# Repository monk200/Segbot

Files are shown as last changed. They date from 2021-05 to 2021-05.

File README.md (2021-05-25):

# Segbot
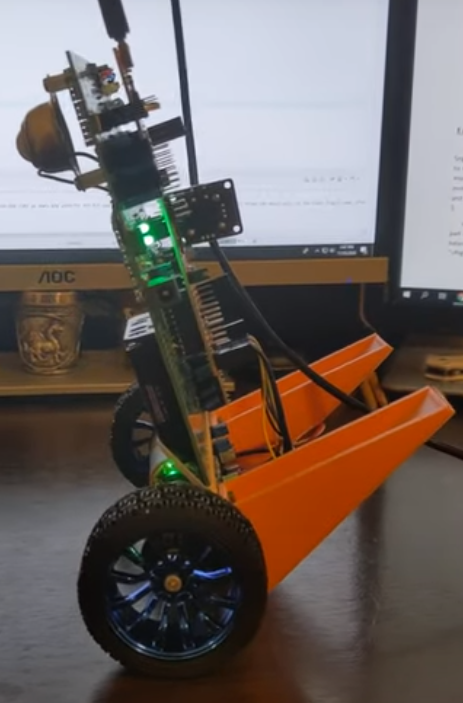
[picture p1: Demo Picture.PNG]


This repository contains files such as code, CAD files, Matlab simulations, and brainstorming documents from my work designing and developing a two-wheeled balancing robot. The project can be split into two main parts: designing the system and developing the real-world version of the system. The original design was done in my [Mechatronics](http://coecsl.ece.illinois.edu/ge423/) course as a final project for Spring 2020 but the real robot was built and programmed in the course [Computer Control of Mechanical Systems](http://coecsl.ece.illinois.edu/me461/) in Fall 2020. Both courses were led by UIUC Prof. Dan Block, the university's Control Systems Lab Manager. Prof. Block created a guide to building a Segbot at [this link](http://coecsl.ece.illinois.edu/segbot/segbot.html) and his guidance and expertise was absolutely essential in all steps of this project.  

## Designing the System
Because of the COVID-19 pandemic, Prof. Block restructured the final project of Mechatronics to be to design a Segbot from scratch. At the time, the [Mechatronics course used the MPS430G2553 microcontroller](https://github.com/monk200/Mechatronics_with_MSP430G2553) so all of the initial design choices and considerations were made keeping that in mind. I compiled a list of parts that were essential for desiging a PCB that would interface with the microcontroller. I was also tasked with creating a CAD model of the robot body and using its parameters, as well as the parameters of the motors, to tune a simulation to balance the Segbot. The last portion of the designing process was to create pseudocode for how the robot needed to behave to balance, solving the inverted pendulum problem. Below you can find a list of each step in the process:  
* [Creating a parts list](https://github.com/monk200/Segbot/blob/main/Parts_Lists/Initial_Parts_List.md): This document includes a list of each part, a link to an online retailor to buy the part, and a link to its datasheet. Most parts also include commentary on the thought process behind choosing the specified part.  
* [Initial wiring configuration](https://github.com/monk200/Segbot/blob/main/Wiring/Initial%20Design%20Wiring%20Diagram.png): This image was created and iterated upon when planning out how the system needs to be connected electronically. This was done as an intermediate step before desiging the PCB in EagleCAD because the color-coding made it quick and easy to troubleshoot and discuss.  
* [PCB design](https://github.com/monk200/Segbot/tree/main/Wiring/Initial%20EagleCAD%20Files): EagleCAD was used to design a PCB that the MSP430 would sit onto. Some parts needed to be created from scratch but otherwise it is a very minimal board.  
* [CAD model](https://github.com/monk200/Segbot/tree/main/Frame/Initial%20Frame%20Design): Autodesk Fusion 360 was used to design a body for the Segbot that would ideally be 3D-printed in UIUC's ISE design lab.  
* [Matlab model](https://github.com/monk200/Segbot/tree/main/Matlab_Simulation/Initial%20Simulation%20Files): A simulation animation and framework were provided by Prof. Block. The parameters from the previous stages of the design process were input into the model and it was manually tuned to balance. This step is useful as a proof-of-concept and as an excersie for students to get experience tuning a control system.  

## Developing the System
While Prof. Block signed off on the original design as feasible, since the second part of this project was done as part of a different course it didn't use the exact same design. Prof. Block upgraded to using the [TMS320F28379D microcontroller](https://github.com/monk200/Mechatronics_with_TMS320F28379D), added a variety of peripherals to the PCB, and simplified the body of the Segbot. For the sake of being thorough, the points below include information on each stage of the design process and how they've changed:  
* [Parts list](https://github.com/monk200/Segbot/blob/main/Parts_Lists/Revised_Parts_List.md): This document lists the essential parts used in the new Segbot design and how they compare to the specs of the previously chosen parts.  
* [Wiring configuration](https://github.com/monk200/Segbot/blob/main/Wiring/Reworked%20Wiring%20Diagram.png): This image is again a color-coded wiring schematic to show a quick layout of how the new components are connected.  
* [PCB design](https://github.com/monk200/Segbot/tree/main/Wiring/Reworked%20EagleCAD%20Files): This folder contains the new EagleCAD files for the PCB. As stated earlier, this is a much more complicated design because a lot of peripherals were added to allow the board to be used for exploring other applications.  
* [CAD model](https://github.com/monk200/Segbot/tree/main/Frame/Reworked%20Frame%20Design): A much simpler design, this design is only two 3D-printed legs to be attached to the PCB itself.  

With a new physical design, the Matlab model needed to be redone but this time since the physical parts were present the tuning was much more reliable. Throughout the [Computer Control of Mechanical Systems](https://github.com/monk200/Mechatronics_with_TMS320F28379D) course, the new microcontroller was explolred and experimented with. Near the end of the semester, I programmed the board to implement control algorithms to solve the inverted pendulum problem and control the robot's motion. The links below lead to details on each step of this process:  
* [Matlab model](https://github.com/monk200/Segbot/tree/main/Matlab_Simulation/Reworked%20SImulation%20Files): Using the same simulation as before but new, more accurate, parameters, I manually tuned the Segbot to balance.  
* [Programming](https://github.com/monk200/Segbot/tree/main/Code): This link goes to the code for the project with extensive details on the processes used and how to set it up on the hardware.  

## Final Product
Below are links to several videos demonstrating different portions of the Segbot's performance:  

### Controlling the Segbot with the Keyboard
Controlling Segbot (https://youtu.be/ZbytxEKrEEE)  
[Github Video Link](https://github.com/monk200/Segbot/blob/main/Working%20Demo%20Video.mp4)  

### Balancing Segbot
Balancing Segbot (https://youtu.be/_FPlLJUeUD4)  

### The Stable Simulation
Stable Simulation (https://youtu.be/3cc0C4fP93k)

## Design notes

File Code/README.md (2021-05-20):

# Programming
This folder finally contains the [code](https://github.com/monk200/Segbot/tree/main/Code/segbot) used to program the TMS320F28379D on Prof. Block's Segbot design to balance and turn accoring to user input through the keyboard. The [code walkthrough](https://github.com/monk200/Segbot/blob/main/Code/code_walkthrough.md) goes through the steps taken to set up the controller and its peripherals as well as a deep focus on the [control algorithms](https://github.com/monk200/Segbot/blob/main/Code/code_walkthrough.md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) used.  

## What the Code Does
As far as the actual code and running it on the Segbot, the only file I personally wrote code in was [segbot_main.c](https://github.com/monk200/Segbot/blob/main/Code/segbot/segbot_main.c), so that's where you can find all of the logic and initializations I've done. It's fairly well commented and organized but the [code walkthrough](https://github.com/monk200/Segbot/blob/main/Code/code_walkthrough.md) includes detailed descriptions, datasheets, and line numbers to guide other people through it. In its current state, the code is set up to balance and turn the Segbot while it is plugged into the computer and being controlled by keyboard inputs. If the microcontroller is flashed and disconnected from the computer, the Segbot will be able to balance but it won't turn (unless you set a constant turn rate in the code, in which case it will continuously spin at that rate).  

## Operating the Segbot
To get the Segbot started, rest it on its legs so the wheels are off the ground and the body is still. Turn the Segbot on by popping the batteries in and then leave it alone to calibrate the sensors for about 4 seconds (a blue LED will be blinking while the sensors calibrate). After this, turn the motors on with the switch and place the Segbot vaguely upright. From there, it will balance itself and be ready to control. Make sure to always turn the motor switch back off before restarting the Segbot.  

## Demo Video
Controlling Segbot (https://youtu.be/ZbytxEKrEEE)

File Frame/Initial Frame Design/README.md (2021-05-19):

# Initial Frame Design
Fusion 360 was used to design the frame, create drawing files, and render images and videos. Since the plan was to 3D print the frame, I wanted to make the dimensions fit inside the ISE product design lab’s Stratasys Dimension SST 1200 3D printer. This means the design had to be smaller than 30x25x25 cm. It also needed to house a battery, the PCB, and account for the motors and wheels. The design ended up being a fairly simple box with pockets inside to be able to set the battery and board into, as well as having front-facing windows to be able to see and quickly access the hardware. The sides of the frame have circular cutouts to fit the motors through and the front and back of the frame have kickstands to keep the Segbot from damaging itself if it fails to balance. The kickstands were highly recommended by Prof. Block because not only do they minimize the damage from the Segbot going off balance but they also provide a stable, repeatable position to calibrate the sensors on startup.  

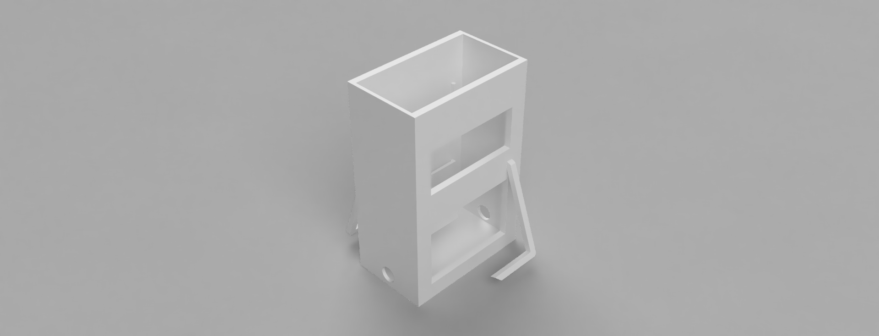
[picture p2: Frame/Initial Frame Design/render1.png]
Render 1
  

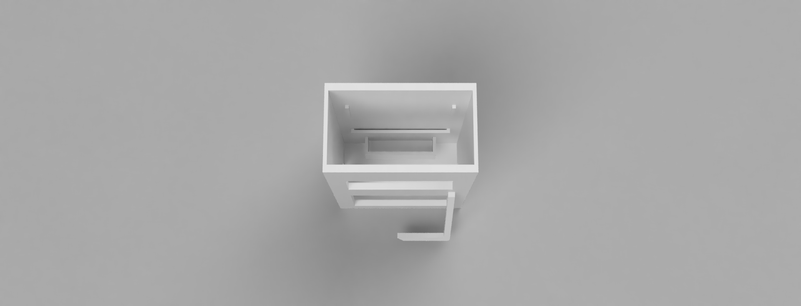
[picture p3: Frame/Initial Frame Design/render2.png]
Render 2
  

## Model Parameters
For the next step of simulating the Segbot in Matlab, the parameters of the physical model will be needed. Fusion provides these and I listed them in [Frame Physical Properties.txt](https://github.com/monk200/Segbot/blob/main/Frame/Initial%20Frame%20Design/Frame%20Physical%20Properites.txt). Below is a summary of the properties:  

* Material:	ABS Plastic
* Mass	1535.286 g
* Center of Mass	-10.00 cm, 13.805 cm, 3.897 cm
* Body Width: 0.20 m
* Body Depth: 0.20 m
* Body Height: 0.29 m
* Distance of the Center of Mass from the Wheel Axis: 11.86 m  

More calculations and their equations will be explained in the [Matlab Model](https://github.com/monk200/Segbot/tree/main/Matlab_Simulation/Initial%20Simulation%20Files) section.

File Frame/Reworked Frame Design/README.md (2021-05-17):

# Reworked Frame Design
Prof. Block simplified the frame design so much so that there isn't really a "frame" left. Instead of designing a protective casing for the hardware, he only designed front-facing legs that the motor subassembly fastens into and then both attach to the PCB. Minimizing the size of this part reduces 3D printer filament needed and makes the Segbot overall more condensed. The battery pack is attached to the back of the PCB by wrapping around the whole thing with a rubber band, which is very secure and manages to not be in the way. Minimizing the design like this also, however, removes the safety of allowing the Segbot to fall backwards when trying to tune the poles. This ended up not being a problem while I was running the program because I always kept a watchful eye on it and used it on smooth, predictable surfaces.  

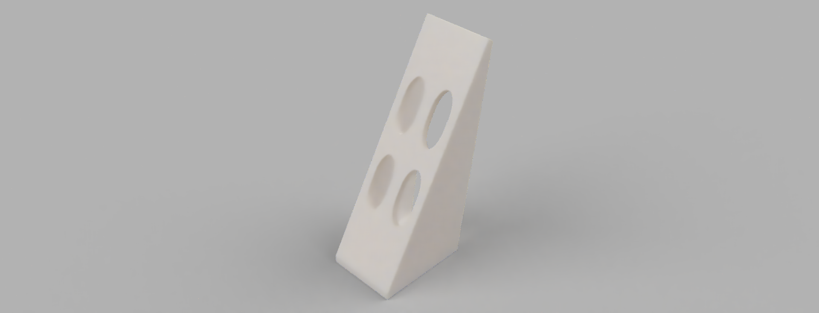
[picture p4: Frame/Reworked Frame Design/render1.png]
Render 1
  

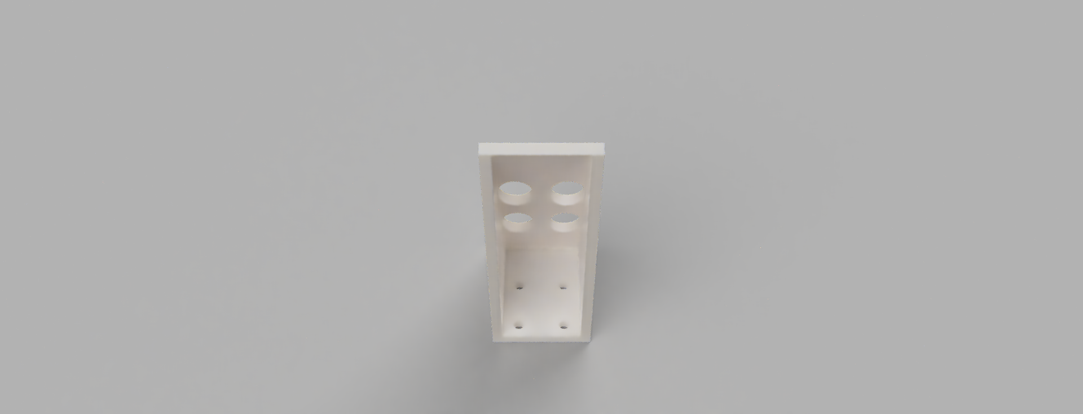
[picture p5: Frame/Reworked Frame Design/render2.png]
Render 2
  

## Model Parameters
For the next step of simulating the Segbot in Matlab, the parameters of the physical model will be needed. Fusion provides these and I listed them in [Frame Physical Properties.txt](https://github.com/monk200/Segbot/blob/main/Frame/Reworked%20Frame%20Design/Frame%20Physical%20Properites.txt). Below is a summary of the properties:  

* Material:	ABS Plastic
* Mass	2.134E+04 g
* Center of Mass	150.00 mm, 319.389 mm, 255.088 mm  

The important parameters shown here are less detailed than in my initial design because of how much smaller this "frame" design is. The two legs on the PCB are going to have much less of an overall effect on the physics of the Segbot than when the bulk of the Segbot's mass before was due to the frame. Also, because this time there were real physical parts to investigate, the Matlab parameters can be measured more directly and are therefore more reliable.

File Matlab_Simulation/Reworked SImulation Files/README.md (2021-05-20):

# Reworked Matlab Simulation
Yorihisa Yamamoto is/was an employee at Mathworks and created a simulation for controlling a self-balancing robot made of Legos. His work creating a Segbot can be found [here](https://www.mathworks.com/matlabcentral/fileexchange/19147-nxtway-gs-self-balancing-two-wheeled-robot-controller-design). For the reworked simulation, the parameters were measured and filled into the model by Prof. Block so there is slightly less information in the section below (but the numbers are significantly more accurate). This simulation was also significantly easier to tune and I was able to both find stable poles for it and manipulate the poles to see how it behaves outside of the stable region.  

## Input Parameters
These parameters should be entered into the appropriate lines at the top of the [<code>equations.m</code>](https://github.com/monk200/Segbot/blob/main/Matlab_Simulation/Reworked%20Simulation%20Files/equations.m) file.  

| Variable | Calculation | Value | Units | Description |
| --- | --- | ---| ---| ---|
| g | - | 9.81 | m/sec^2 | Gravity acceleration |
| m | wheel weight + Mrotor | 0.0615 | kg | Wheel weight |
| R | - | 0.067 | m | Wheel radius |
| Jw | [m * (R^2)] / 2 | 1.3804e-4 | kg * m^2 | Wheel inertia moment |
| M | - | 0.5764 | kg | Body weight |
| L | - | 0.049 | m | Distance of center of mass from the wheel axis before motors |
| Jpsi | M * (L^2) / 3 | 4.6131e-4 | kg * m^2 | Body pitch inertia moment |
| Jm | Jmotor * (gear ratio ^2) | 2.285e-4 | kg * m^2 | DC motor inertia moment |
| Rm | - | 1.875 | ohm | DC motor resistance |
| Kb | Kt (assumption) | 0.30646 | V sec/rad | DC motor back EMF constant |
| Kt | - | 0.30646 | Nm/A | DC motor torque constant |
| n | - | 1 | - | Gear ratio |
| fm | assumption | 0.0022 | - | Friction coefficient between body and DC motor |
| fw | assumption | 0 | - | Friction coefficient between wheel and floor |

## Tuning the Simulation
Continuing work in the [<code>equations.m</code>](https://github.com/monk200/Segbot/blob/main/Matlab_Simulation/Reworked%20Simulation%20Files/equations.m) file, the last line defines <code>K</code>. This set of simulation files only has the three-state files available. This means that the only K gain to edit is <code>K</code> and the Simulink file that should be used is [<code>segbot.slx</code>](https://github.com/monk200/Segbot/blob/main/Matlab_Simulation/Reworked%20Simulation%20Files/segbot.slx).  

Typing <code>eig(A-B*K)</code> into the Command Window will output the eigenvalues of the 3-state system with the current K gains. When this is done with the gains currently listed in the file, the eigenvalues are [-446.4162, -8.9051, -0.9308]'. These poles are stable, which can be checked by noticing that all the poles are in the left half plane and that the simulation does balance the Segbot. To change the poles, use the place function in Matlab with <code>K = place(A, B, poleArray)</code>.  

The Simulink file can also be edited to adjust the type of disturbance applied to the system. The Pulse Generator block labeled "Finger Pushing At Top of Body (Newtons)" can be edited to increase the amplitude, corresponding to the pushing force. The other parameters can also be edited but for basic stability the goal is to tune the Segbot to stabilize after a 4.5 N tap. By default, the Simulink file only has the tap set to be 0.5 N.  

## Results
The current poles set in the Matlab file are stable for the system, and the running simulation can be seen in the video below. Below there is also an image of the three plots being monitored to ensure a stable system. You can see how in the Psi_body plot below, the body of the Segbot waivers but stabilizees in less than 4 seconds, with very little overshoot. The Theta Wheel plot shows how the wheels rotate as they work to correct Psi_body but they do not rotate when the Segbot finds its balancing point. Lastly, the motor voltage plot shows that the control effort stays within a reasonable range (between 6V and -6V in this model) and does not waiver back and forth. All of these plots support that this is a stable system.  

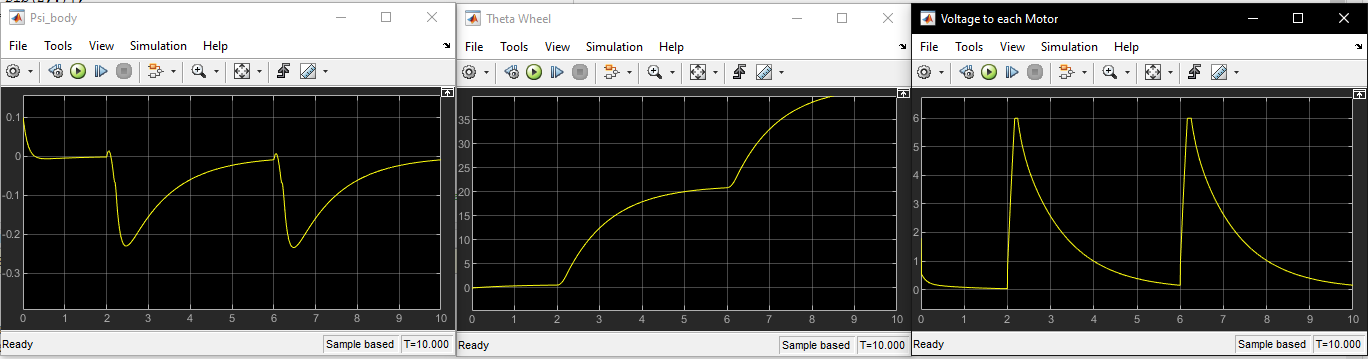
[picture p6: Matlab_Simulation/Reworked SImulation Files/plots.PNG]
Stable Pole Plots
  

[Simulation Video on Github](https://github.com/monk200/Segbot/blob/main/Matlab_Simulation/Reworked%20SImulation%20Files/Stable%20Poles.mp4)  

Stable Simulation (https://youtu.be/3cc0C4fP93k)  

## Further Analysis
### Increasing Responsiveness
Further analysis on the simulation can be done to understand how the system works and how it behaves with different poles. First I tried setting the K gains to be noticably more responsive than the stable gains. Setting <code>K = [-34.3159, -3.6375, -3.3290]</code> produces poles at [-446.4162, -8.9051, -10]'. Below again are plots and a link to a video of the simulation running. The Psi_body plot already shows how there is a much more dramatic adjustment of the Segbot's tilt, but it still is able to stabalize. The portions of Theta Wheel where the Segbot is adjusting its position are much faster, also meaning that the distance doesn't need to be as large to create a counter-balancing force. The biggest issue with these gains can be seen in the motor voltage plot. The control input actually saturates very slightly at 6V, the maximum voltage the motor simulation can handle. (At this point it is worthwhile to note that the simulation motor voltage is scaled down from a 10V maximum to 6V) There is also an overshoot into the negative voltages to handle the initial control effort overshooting the amount of speed needed.  

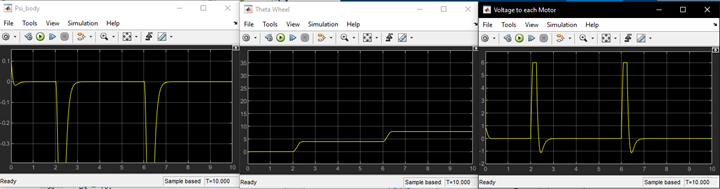
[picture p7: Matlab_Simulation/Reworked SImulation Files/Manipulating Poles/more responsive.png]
More Responsive Poles Plots
  

More Responsive Simulation (https://youtu.be/d-1ndJblGV4)  

Increasing the responsiveness of the system even more can show even more dramatic issues. This amount of responsiveness can be dangerous to even try on real hardware because the control effort has the potential to burn out the motors or cause other undue stress on the parts. Here <code>K = [-63.5382, -8.7203, -10.4572]</code> making the poles [-446.4162, -15, -20]'. The plots still show that the Segbot comes back to equilibrium but the dramatic oscilation sseen on the Psi_body plot and the motor voltage plot show clear issues. The sharp changes are hard to control and end up causing a lot of overshoot. Not to mention, the motor voltage saturates in both the positive and negative direction (this is what would burn out the motors on real hardware).  

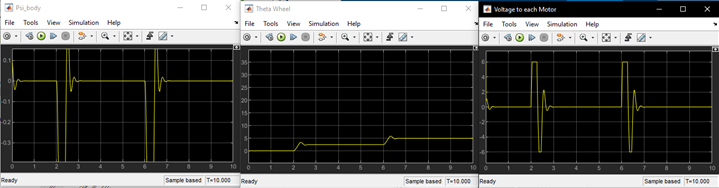
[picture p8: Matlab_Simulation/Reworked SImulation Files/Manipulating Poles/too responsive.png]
Too Responsive Poles Plots
  

Too Responsive Simulation (https://youtu.be/qGNAavwwsLA)  

### Decreasing Responsiveness
As a last excersise with manipulating the poles of the system, next I made the system not responsive enough. I set <code>K = [-47.2416, -13.2226, -18.4865]</code> which made the poles [-80, -50, -60]'. The plots for this system show an insane amount of oscillation. In fact, in the plots there is a point just before the 3 second mark where it just barely starts to approach its balancing point and then it recieves the second tap which adds enough energy that the controller can't keep the Segbot from tipping over entirely. Because of how dramatic the oscillations are, the motor voltage saturates again trying to rescue it from its inevitable fate.  

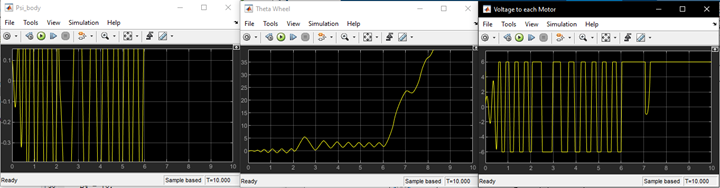
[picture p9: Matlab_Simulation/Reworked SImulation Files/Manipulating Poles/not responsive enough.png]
Not Responsive Poles Plots
  

Not Responsive Simulation (https://youtu.be/98DRiGnAHTE)  

### Manipulating Segbot Motion
Returning back to using the stable poles, the simulation can still be changed to explore other behaviors of the controller. If the "Finger Pushing At Top of Body (Newtons)" block is changed to have a 50% pulse width and an amplitude of 0.4 N, it will simulate pushing the Segbot gently for 2 seconds. The video below shows how the Segbot pushes back on the "finger" (the force is applied from the left) to stay balanced. This makes sense because it needs to counteract the force being applied to stay upright.  

Pushing the Segbot (https://youtu.be/trDw0ImDjyA)  

Now, setting the amplitude of the same block to 0 N and editing the "Psi Offset" block in the bottom right of the Simulink file to 0.2 radians will tell the Segbot to drive forward for 2 seconds. The video below shows how when the Segbot gets the initial moment of movement, its body leans forward and quickly adjusts back. It also leans backwards for a moment when it stops moving to counteract the forces caused by being in motion and then stopping.  

Driving Forward (https://youtu.be/pj7e5s4WAzk)  

These analysis are all useful in gaining a deeper understanding of how the control algorithm behaves and highlighting the physics of how an inverted pendulum needs to be balanced.

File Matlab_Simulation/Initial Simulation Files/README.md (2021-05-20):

# Initial Matlab Simulation
Yorihisa Yamamoto is/was an employee at Mathworks and created a simulation for controlling a self-balancing robot made of Legos. His work creating a Segbot can be found [here](https://www.mathworks.com/matlabcentral/fileexchange/19147-nxtway-gs-self-balancing-two-wheeled-robot-controller-design). Some of the parameters in the simulation are educational guesses and others don't translate very well unless the Segbot design is similar to Yamamoto's design. Nonetheless, it helps create a proof-of-concept that balancing a similar Segbot will work and allows students to experience tuning a balancing controller without needing the physical hardware. Since the first portion of this project had to be done remotely and with no hardware, the parameters are estimated and I did my best to tune the simulation. Ultimately, the simulation is still unstable after many hours of trying different pole placements but I hypothesize this is because the parameters are not accurate enough or because the frame of the Segbot makes it much more difficult to balance.  

## Input Parameters
The parameters below were estimated and calculated as well as possible given the sometimes surprisingly limited information on the previously chosen parts. The motor parameters specifically, however, were estimated using real-world information provided by Prof. Block about a similar motor. These parameters should be entered into the appropriate lines at the top of the [<code>equations.m</code>](https://github.com/monk200/Segbot/blob/main/Matlab_Simulation/Initial%20Simulation%20Files/equations.m) file. Not all of these parameters are listed in the file but all of them were calculated for the sake of data collection.  

| Variable | Calculation | Value | Units | Description |
| --- | --- | ---| ---| ---|
| g | - | 9.81 | m/sec^2 | Gravity acceleration |
| m | 0.03 (estimated wheel weight) + 0.032 (given Mrotor) | 0.062 | kg | Wheel weight |
| R | - | 0.0325 | m | Wheel radius |
| Jw | [m * (R^2)] / 2 | 3.2744e-5 | kg * m^2 | Wheel inertia moment |
| M | 0.197 (battery) + 2 * 0.982 (both motors) + 0.04 (estimated PCB + components) + 0.066 (given Mstator) + 1.746 (frame) | 2.245 | kg | Body weight |
| W | - | 0.20 | m | Body width |
| D | - | 0.20 | m | Body depbth |
| H | - | 0.29 | m | Body height |
| L | sqrt[(13.805-2)^2 + (5-3.897)^2] | 11.86 | m | Distance of center of mass from the wheel axis before motors |
| Jpsi | M * (L^2) / 3 | 105.2603 | kg * m^2 | Body pitch inertia moment |
| Jphi | M * (W^2 + D^2) / 12 | 0.1796 | kg * m^2 | Body yaw inertia moment |
| Jm | (given Jmotor) * (gear ratio ^2) = 1.1e-7 * (1/45)^2 | 5.432e-11 | kg * m^2 | DC motor inertia moment |
| Rm | 12V / 1.8A | 6.667 | ohm | DC motor resistance |
| Kb | Kt (assumption) | 0.4903 | V sec/rad | DC motor back EMF constant |
| Kt | 9 kg * cm / 1.8A | 0.4903 | Nm/A | DC motor torque constant |
| n | - | 1 | - | Gear ratio |
| fm | assumption | 0.0022 | - | Friction coefficient between body and DC motor |
| fw | assumption | 0 | - | Friction coefficient between wheel and floor |

## Tuning the Simulation
Continuing work in the [<code>equations.m</code>](https://github.com/monk200/Segbot/blob/main/Matlab_Simulation/Initial%20Simulation%20Files/equations.m) file, the last two lines define <code>K3</code> and <code>K</code>. For this case, focus on the 3-state system. This means that the only K gain to edit is <code>K3</code> and the Simulink file that should be used is [<code>segbot3state.slx</code>](https://github.com/monk200/Segbot/blob/main/Matlab_Simulation/Initial%20Simulation%20Files/segbot3state.slx).  

Typing <code>eig(A3-B3*K3)</code> into the Command Window will output the eigenvalues of the 3-state system with the current K3 gains. When this is done with the gains currently listed in the file, the eigenvalues are [1136.6, 0.80, -0.80]', which makes the system unstable because the third pole is the only one in the left half plane. This can be visually verified by running the Simulink file. To try to stabilize the system, use the place function in Matlab to place the poles in the left half plane directly. The syntax for this would be <code>K3 = place(A3, B3, poleArray)</code>.  

The Simulink file can also be edited to adjust the type of disturbance applied to the system. The Pulse Generator block labeled "Finger Pushing At Top of Body (Newtons)" can be edited to increase the amplitude, corresponding to the pushing force. The other parameters can also be edited but for basic stability the goal is to tune the Segbot to stabilize after a 4.5 N tap.  

## Results
Unfortunately, I was not able to find stable poles for the system even after hours of trying. This could be because my estimates for the model were too inaccurate or because the physical design itself is not easy to balance. The most likely way that the parameter estimates are off is that more calculations need to be made with respect to where each part is stored in the Segbot frame. The design has enough space that the weight is not centered over the wheel axis and the mass is more distributed. Another point that I didn't consider when creating the frame model is that a top-heavy object is actually easier to balance than a bottom-heavy object because it requires a smaller control input. This was not modeled in the simulation but the frame does design for the battery to sit low, which might have made the sweet spot for balance more difficult to achieve in the real world.  

Prof. Block was working with me throughout each step of the design process and approved of each of my finalized choices up to just before working with the simulation. This makes me confident that despite some potentially non-optimal choices, this Segbot design is still capable of working in real life and with some minor improvements. Below is a link to a video of the simulation when it was as stabilized as I managed to get it. I did not end up saving the poles for this behavior because they still needed a notable amount of changes to be viable.  

Initial Simulation (https://youtu.be/ORlbtnldfrQ)

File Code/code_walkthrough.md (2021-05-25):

# Segbot Code Walkthrough
This file will be going through the steps and logic to how the Segbot code works, mostly glossing over how different peripherals of the microcontroller are initialized. The [code](https://github.com/monk200/Segbot/blob/main/Code/segbot/segbot_main.c) itself is well commented and written in a way that most of the peripherals I know how to implement are set up, making it easy to change the code for other functions. Because of this, however, if this code is run on a barebones system just intended to be a Segbot then it will have issues (because certain parts on my PCB and written into my code aren't directly for the Segbot). To learn more about how to interface with the TMS320F28379D or the other parts, I recommend looking through the [datasheets provided](https://github.com/monk200/Segbot/blob/main/Parts_Lists/Revised_Parts_List.md).  

These sections are in the order necessary for the next step in the logic, not necessarily the order they appear in the [code](https://github.com/monk200/Segbot/blob/main/Code/segbot/segbot_main.c). The line numbers will be mentioned at certain points to make it easier to follow and reference the text.  

## Initialize ADCA to push MPU-9250 data onto SPI queue
### Initialize SPIB to read from the MPU-9250
Lines [267](https://github.com/monk200/Segbot/blob/675fc0f092b4d83fd8ebe73bdf923763511bc55d/Code/segbot/segbot_main.c#L267), [824-1001](https://github.com/monk200/Segbot/blob/675fc0f092b4d83fd8ebe73bdf923763511bc55d/Code/segbot/segbot_main.c#L824)  

>Prof. Block provided this [condensed SPI datasheet](http://coecsl.ece.illinois.edu/me461/Labs/SPICondensed_TechRef.pdf) with skeleton code for initializing the SPI to communicate with the IMU. The datasheet includes descriptions of what each bit in each bitfield of the SPI corresponds to. All of the comments in <code>setupSpib()</code> has comments describing what code needed to be written and it can be used in conjunciton with the datasheet to see why. The execption is the code on lines [917-995](https://github.com/monk200/Segbot/blob/675fc0f092b4d83fd8ebe73bdf923763511bc55d/Code/segbot/segbot_main.c#L917), which was entirely provided by Prof. Block.  

### Initialize EPWM5 to trigger ADCA
Lines [307](https://github.com/monk200/Segbot/blob/675fc0f092b4d83fd8ebe73bdf923763511bc55d/Code/segbot/segbot_main.c#L307), [723-738](https://github.com/monk200/Segbot/blob/675fc0f092b4d83fd8ebe73bdf923763511bc55d/Code/segbot/segbot_main.c#L723)  

>EPWM5 is set up as a timer that triggers the ADCA sample every 1ms. Similar to before, Prof. Block provided pseudocode for how to set up an EPWM register as an ADC trigger and provided a [technical reference](http://coecsl.ece.illinois.edu/me461/Labs/EPWM_Peripheral.pdf) for the EPWM peripheral.  

Lines [308](https://github.com/monk200/Segbot/blob/675fc0f092b4d83fd8ebe73bdf923763511bc55d/Code/segbot/segbot_main.c#L308), [741-809](https://github.com/monk200/Segbot/blob/675fc0f092b4d83fd8ebe73bdf923763511bc55d/Code/segbot/segbot_main.c#L741)  

>A large chunk of this function is commented out because it is skeleton code for setting up the other ADC channels. ADCA is set up to SOC0 and SOC1 trigger ADCA2 and ADCA3, respectively. This specific sampling exists because one of the extra features on my board is a joystick, however this is not used in the final Segbot (but it could be!). Regardless of what is being sampled, it is necessary to sample the ADC every 1ms to trigger the next step. Lines [769](https://github.com/monk200/Segbot/blob/675fc0f092b4d83fd8ebe73bdf923763511bc55d/Code/segbot/segbot_main.c#L769) and [772](https://github.com/monk200/Segbot/blob/675fc0f092b4d83fd8ebe73bdf923763511bc55d/Code/segbot/segbot_main.c#L772) are where EPWM5 is selected as the timer. More information on the choen values for the other parts of the ADC setup can be found in Prof. Block's [ADC technical reference](http://coecsl.ece.illinois.edu/me461/Labs/ADC_Peripheral.pdf).  

### Use ADCA interrupt to transmit MPU-9250 data
Lines [452-479](https://github.com/monk200/Segbot/blob/675fc0f092b4d83fd8ebe73bdf923763511bc55d/Code/segbot/segbot_main.c#L452)  

>As stated above, the channels being read of the ADC aren't actually used in the final Segbot so the first few lines of this funciton can be ignored. However, from line [462-473](https://github.com/monk200/Segbot/blob/675fc0f092b4d83fd8ebe73bdf923763511bc55d/Code/segbot/segbot_main.c#L462), The SPI transmit buffer reads off all of the accelerometer and gyroscope readings (including a few junk values). The choices here can be explained more by reading the [MPU-9250 technical reference](http://coecsl.ece.illinois.edu/me461/Labs/MPU-9250-Addendum.pdf). Essentially, the bits corresponding to the desired signals are put onto a queue that the SPI will read from later.  

## Setup EPWM6A and EPWM6B to control the left and right motors
### Setup Quadrature Encoder
Lines [268](https://github.com/monk200/Segbot/blob/675fc0f092b4d83fd8ebe73bdf923763511bc55d/Code/segbot/segbot_main.c#L268), [679-720](https://github.com/monk200/Segbot/blob/675fc0f092b4d83fd8ebe73bdf923763511bc55d/Code/segbot/segbot_main.c#L679)  

>The code to setup the eQEP peripherals was mostly provided by Prof. Block, but he also commented that this simple use of the eQEP was almost entirely provided by sample code that came with the microcontroller. Nonetheless, it is absolutely required before the next step in the process.  

### Create functions to read from the encoders
Lines [390-410](https://github.com/monk200/Segbot/blob/675fc0f092b4d83fd8ebe73bdf923763511bc55d/Code/segbot/segbot_main.c#L390)  

>Prof. Block provided all but the last line in each function. The goal of these functions are to return the radians that the wheel is currently at (relative to their position at startup). To determine this, I was given the information that the gear ratio is 18.7, meaning that 18.7 rotations of the motor cause one rotation of the wheel. I was also told that the eQEP creates a square wave based on when one of the 20 North/South magnetic poles spaced around the wheel passes by a Hall Effect sensor. Since the eQEP is set to be in quadrature count mode, the number of counts per revolution is 4 * 20 = 80. This can be combined with the gear ratio to find the conversion factor from eQEP counts to radians. This is done with the equation EQep1Regs.QPOSCNT * (TWOPI/(80 * 18.7)), and the polarity would be negative for the left motor and positive for the right.  

### Initialize EPWM6A and EPWM6B
Lines [351-372](https://github.com/monk200/Segbot/blob/675fc0f092b4d83fd8ebe73bdf923763511bc55d/Code/segbot/segbot_main.c#L351)  

>Similarly to [setting up EPWM5](https://github.com/monk200/Segbot/new/main/Code#initialize-epwm5-to-trigger-adca), the [EPWM technical reference](http://coecsl.ece.illinois.edu/me461/Labs/EPWM_Peripheral.pdf) can be used to set up EPWM6A and EPWM6B to control the motor speeds. Their period needs to be set to a 20 kHz carrier frequency and their duty cycle will be used to control their speed.  

### Create functions to set the speed of the motors
Lines [412-435](https://github.com/monk200/Segbot/blob/675fc0f092b4d83fd8ebe73bdf923763511bc55d/Code/segbot/segbot_main.c#L412)  

>These functions take in a <code>controleffort</code> variable. They need to start by saturating the control to be between -10 and 10, corresponding to the minimum and maximum reasonable operating speeds for the motors. After that, either GPIO29 or GPIO32 (depending on which motor) is set to a binary value representing if the motor is moving forward, which is true if the control effort is positive. The last line of each function scales the control effort to the period of the register and sets that value as the duty cycle. One difference in my code from what most people's code should look like is that right wheel encoder had an inconsistency in wiring so the polarity is opposite of what it should be. This is compensated for in my code but any recreations of this project should be careful to test that the motors are moving in the direction the user intends them to be before moving forward with the control algorithms.  

## Use the SPIB interrupt to calibrate MPU-9250 and gather filtered values over time
Lines [482-581](https://github.com/monk200/Segbot/blob/675fc0f092b4d83fd8ebe73bdf923763511bc55d/Code/segbot/segbot_main.c#L482)  

>The first thing the SPIB interrupt does when it is called every 1ms is read the MPU-9250 values off the SPI queue. These raw values are converted so that the accelerometer readings range from -4g to 4g and the gyroscope readings range from -250 degrees/sec to 250 degrees/sec. Just before entering the calibration stage, it also reads the current position of each wheel (again accounting for the pinout inconsistency on my encoder).  

### Calibration
Lines [509-533](https://github.com/monk200/Segbot/blob/675fc0f092b4d83fd8ebe73bdf923763511bc55d/Code/segbot/segbot_main.c#L509)  

>The calibration of the MPU-9250 starts by just taking two seconds to let any electrical noise caused by startup calm down (calibration_state = 0). After those two seconds, it spends another two seconds just summing the reading for each parameter. At the end of this state, it takes the average over that two second period and sets it as the parameter's corresponding offset (calibration_state = 1). This process happens upon startup so it is important to keep the Segbot steady for at least 4 seconds (there will be a blue LED that blinks during the calibration process, [line 572](https://github.com/monk200/Segbot/blob/675fc0f092b4d83fd8ebe73bdf923763511bc55d/Code/segbot/segbot_main.c#L572)).  

### Kalman Filter
Lines [534-569](https://github.com/monk200/Segbot/blob/675fc0f092b4d83fd8ebe73bdf923763511bc55d/Code/segbot/segbot_main.c#L534)  

>A Kalman filter is used to combine the accelerometer reading and the integral of the gyroscope. The accelerometer provides a tilt reading but it is slow and therefore not responsive enough to let the control algorithm balance the Segbot. The integral of the gyroscope provides a tilt rate much faster, but its downside being that it starts drifting eventually because of electrical noise. Using the Kalman filter to combine the two allows for an accurate and fast reading of the tilt. At the end of this function, since the SPI is called every 1ms and the control algorithm is only called every 4ms, the average of the last 4ms of data is updated and passed onto the control algorithm.  

## Use software interrupt to implement control algorithms
### Balancing control
Lines [584-597](https://github.com/monk200/Segbot/blob/675fc0f092b4d83fd8ebe73bdf923763511bc55d/Code/segbot/segbot_main.c#L584)  

>The balancing control starts by applying a low-pass filter in discrete time to estimate the velocity of each wheel. Magnetic encoders have a low amplitude and the noise in the position variable is amplified when differentiated, so blocking out higher frequencies lead to more accurate estimates of the velocity. In my implementation, I applied a low-pass filter with a cutoff frequency of 125 rad/s, the bode plot of which can be seen below. It it worthwhile to note here that the cutoff frequency is a tunable parameter and the Segbot performance can be changed by changing it. Also below is a snippet of the Matlab code used to take the derivative of the filter and then convert it to discrete time using the Tustin rule (aka bilinear transformation aka trapezoidal rule) at a 4ms sample rate. This final equation, <code>vel_pos</code>, can be converted so that the <code>z</code> is to the power of -1, making it refer to a unit delay. This is necessary in real-time application because at any given moment we only know the past states. The final form of the equation can be seen in the code on [lines 592 and 593](https://github.com/monk200/Segbot/blob/675fc0f092b4d83fd8ebe73bdf923763511bc55d/Code/segbot/segbot_main.c#L592).  

<p align="center">
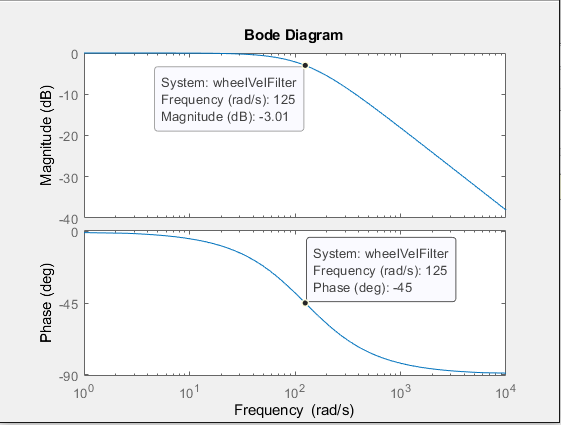
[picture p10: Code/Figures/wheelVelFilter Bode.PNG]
Bode Plot
  
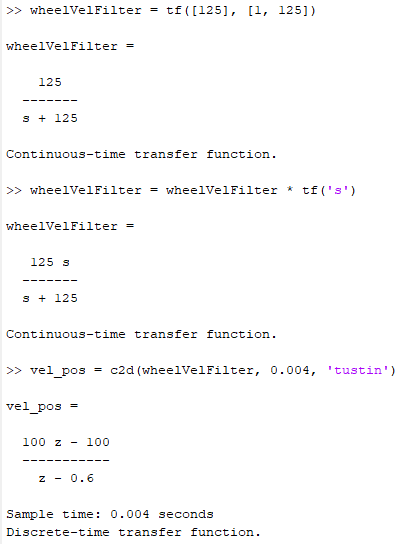
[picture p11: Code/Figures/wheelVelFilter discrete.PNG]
  
  Expanded Equation
</p>  

>After estimating the current velocity of the left and right wheels, the actual balancing control needs to be added. For this, I used a full state feedback control where x<sub>1</sub> is tilt, x<sub>2</sub> is tilt rate, and x<sub>3</sub> is the average of the two (now filtered) wheel velocities. This portion of the equations were derived by [Yorihisa Yamamoto's Segobt paper](https://www.mathworks.com/matlabcentral/fileexchange/19147-nxtway-gs-self-balancing-two-wheeled-robot-controller-design) and can be found in the code for the [Matlab model](https://github.com/monk200/Segbot/tree/main/Matlab_Simulation) used previously. Ultimately, the control effort u = -K<sub>1</sub>x<sub>1</sub> - K<sub>2</sub>x<sub>2</sub> - K<sub>3</sub>x<sub>3</sub>, where each variable K is a tunable gain. The implementation of this in the code is on [line 596](https://github.com/monk200/Segbot/blob/675fc0f092b4d83fd8ebe73bdf923763511bc55d/Code/segbot/segbot_main.c#L596). As far as tuning the gains, the [Matlab simulation](https://github.com/monk200/Segbot/tree/main/Matlab_Simulation/Reworked%20SImulation%20Files) was used as a starting point (and those gains need to be scaled up to to real-world Segbot) but because of discrepencies between the simulated model and the real model, the values may need to be tuned further on the real robot. For my robot, the gains K<sub>1</sub> = -30, K<sub>2</sub> = -2.8, K<sub>3</sub> = -1.0 worked sufficiently but can still be improved to reduce the small oscillations happening in the video below (which are slightly caused by the cable dragging anyway). The gains I had used in my simulation ([-34.3159, -3.6375, -3.3290]) also balanced but seemed to be slightly less stable. The parameter that actually seemed to have more of an impact when tuned was [the angle the body of the Segbot tries to balance at](https://github.com/monk200/Segbot/blob/675fc0f092b4d83fd8ebe73bdf923763511bc55d/Code/segbot/segbot_main.c#L77).  

Balancing Segbot (https://youtu.be/_FPlLJUeUD4)  

### Steering control
Lines [600-622](https://github.com/monk200/Segbot/blob/675fc0f092b4d83fd8ebe73bdf923763511bc55d/Code/segbot/segbot_main.c#L600)  

>The process of starting the steering control starts similarly to calculating wheel velocity. The steering control essentially commands the Segbot to turn at a certain rate by aiming to a achieve a certain difference between the left and right wheel velocities. To do this, I started by using a low-pass filter with a cutoff frequency of 250 rad/s and converting it to discrete time at a 4ms sample rate again. The steps from the last filter are taken and shown below, to finally produce the code in [line 602](https://github.com/monk200/Segbot/blob/675fc0f092b4d83fd8ebe73bdf923763511bc55d/Code/segbot/segbot_main.c#L602).  

<p align="center">
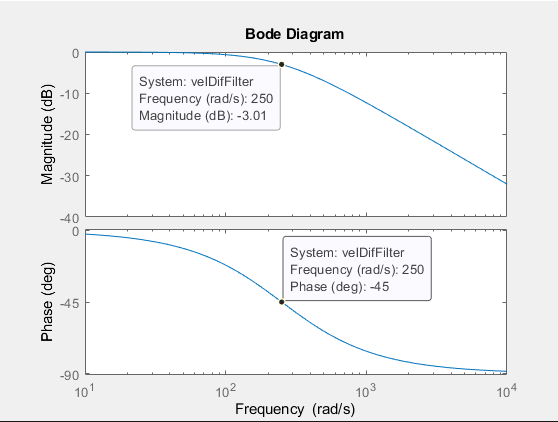
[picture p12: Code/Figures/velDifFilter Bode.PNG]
Bode Plot
  
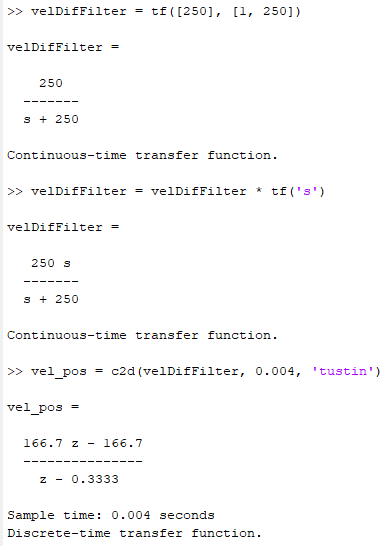
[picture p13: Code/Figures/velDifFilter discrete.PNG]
  
  Expanded Equation
</p>  

>Next, the error between the desired angle to turn to and the difference between the two wheel positions in radians is integrated using the trapezoidal rule ([line 605](https://github.com/monk200/Segbot/blob/675fc0f092b4d83fd8ebe73bdf923763511bc55d/Code/segbot/segbot_main.c#L605)). Doing these calculations produces the necessary variables to perform PID control of the turn. The turn command ends up being K<sub>p</sub> * turnError + K<sub>i</sub> * turnErrorIntegral - K<sub>d</sub> * diffInWheelVels ([line 606](https://github.com/monk200/Segbot/blob/675fc0f092b4d83fd8ebe73bdf923763511bc55d/Code/segbot/segbot_main.c#L606)).  

>Before applying the turn command determined by the PID algorithm, it needs to both account for integral windup and be saturated so that it doesn't overpower the balance control. Integral windup happens when for some reason the error term in the algorithm keeps growing, often caused when the motor can't meet the desired control effort. We demonstrated this in the lab by holding onto one of the wheels and then when you release it, it goes extremely fast because it is trying to correct for a huge percieved error. A more stable system doesn't attempt to correct itself so aggressively because it can damage the motor or throw the Segbot off balance. In this case, the code will stop the error integral from accumulating if the turn command is near its maximum value. When the turn command is near the maximum value, there is no reason to keep accumulating the error integral because the error is already right at the maximum error the Segbot can account for. As far as saturting the control, the code keeps the turn command within [-4, 4] so that it never overpowers the balancing control that ranges from [-10, 10]. A block diagram of the turning algorithm can be seen below: 

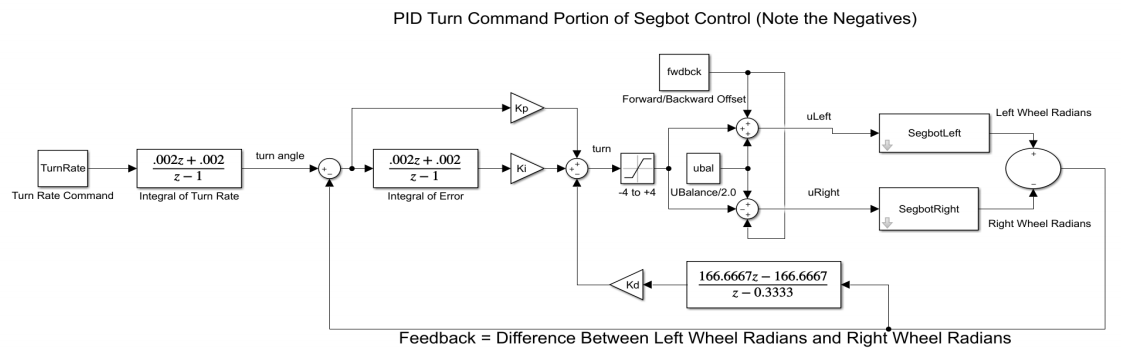
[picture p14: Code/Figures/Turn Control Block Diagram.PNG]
Turn PID
  

>Finally, on [lines 614-622](https://github.com/monk200/Segbot/blob/675fc0f092b4d83fd8ebe73bdf923763511bc55d/Code/segbot/segbot_main.c#L614), the balacing control effort, turning control effort, and direction commands are combined, saturated to be between -10 and 10, and sent to the left and right motor control functions. The last portion of the software interrupt just updates all of the past states for the next time the software enters the interrupt to calculate a new control effort. A video of me controlling the Segbot's motion using keyboard input can be seen below:  

Controlling Segbot (https://youtu.be/ZbytxEKrEEE)  

## Sources
https://www.bzarg.com/p/how-a-kalman-filter-works-in-pictures/  
https://towardsdatascience.com/kalman-filter-an-algorithm-for-making-sense-from-the-insights-of-various-sensors-fused-together-ddf67597f35e  
https://doc.synapticon.com/software/42/motion_control/advanced_control_options/filtering/low-pass-filter/index.html  
https://www.electrical4u.com/cutoff-frequency/  
https://www.allaboutcircuits.com/technical-articles/deriving-and-plotting-a-low-pass-transfer-function-on-matlab/  
https://control.com/technical-articles/intergral-windup-method-in-pid-control/

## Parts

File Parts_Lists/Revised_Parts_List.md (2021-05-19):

# Parts List for the Revised Design
The revised design was made by Prof. Block and I've deconstructed it here and in the [wiring diagram](https://github.com/monk200/Segbot/blob/main/Wiring/Reworked%20Wiring%20Diagram.png) to isolate the essential parts needed just for the Segbot project. There are many similarities between my initial design and Prof. Block's design with the only major changes being to the microcontroller and the frame. Below I go through each part used in Prof. Block's design and I compare his choices to mine with commentary on how these changes improve the Segbot.  

## Microcontroller
The biggest change in the new design is that it is using the TMS320F28379D microcontroller (on the TI development board). Both the MSP430 and the TMS320F28379D are part of TI's C2000 series but this board has a lot more pins and peripherals, making it a good upgrade for leaning about embedded systems and making more complex projects. One of the challenges with the initial design was that there were so few pins that wiring had to be carefully planned out. Some other chips in the last system had some of their pins either completely disconnected or tied to ground because there wasn't the luxury of extra pins. During conversations about the initial design I even mentioned potentially making the control wireless or adding a camera, both of which would have been very difficult to manage with the three pins left over after connecting the essential elements.  

The TMS320F28379D has two 32-bit CPUs, 204 KB SRAM, 50 I/O pins, between 12-24 ADC channels at either a 16 or 12 bit resolution, and three built-in quadrature encoders. Prof. Block compiled a cheat-sheet for navigating the differnt uses of each pin, which can be found [here](https://github.com/monk200/Segbot/blob/main/Wiring/TMS320F28379D%20Pinout%20Info/PinMuxTableF28379DLaunchPad.pdf). Below are a couple images of the layout of the launchpad board used:  
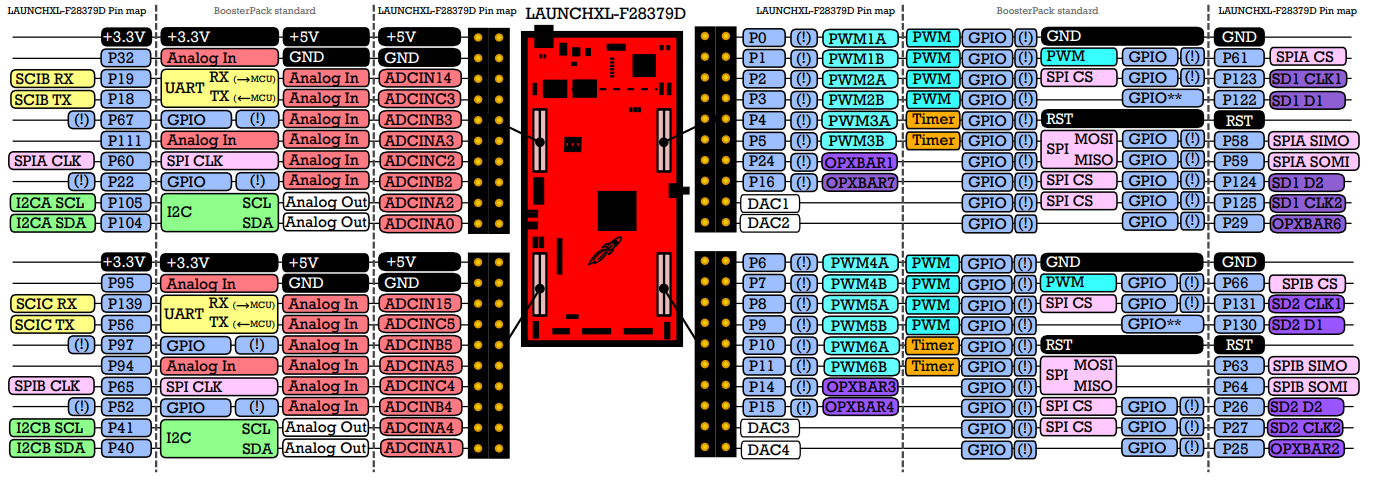
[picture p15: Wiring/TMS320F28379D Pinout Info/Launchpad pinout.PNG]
TMS320F28379D Pinout
  
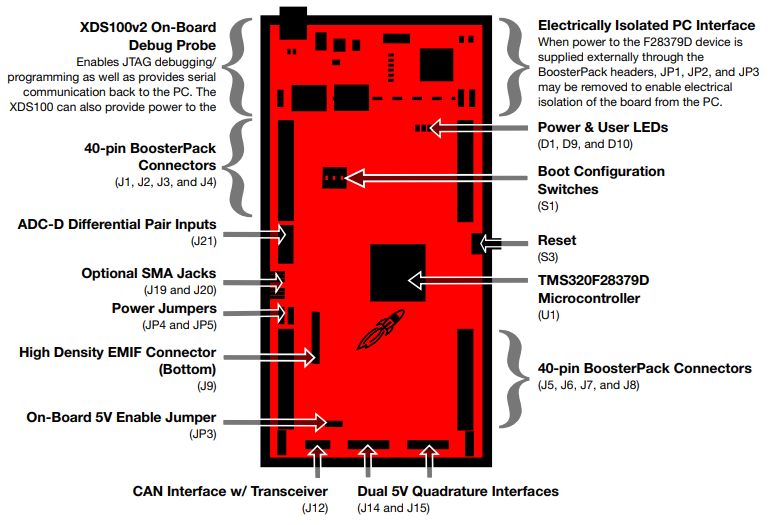
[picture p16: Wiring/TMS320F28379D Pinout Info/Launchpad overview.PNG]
Launchpad Layout
  

[Texas Instruments Page](https://www.ti.com/tool/LAUNCHXL-F28379D)  
[Chip Datasheet](https://www.ti.com/lit/ds/sprs880o/sprs880o.pdf?ts=1621420796409)  
[Launchpad Datasheet](https://www.ti.com/lit/an/sprt720/sprt720.pdf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)  
[Store page](https://www.digikey.com/en/products/detail/texas-instruments/LAUNCHXL-F28379D/7219341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)  

Cost: $41 on digikey.com, $0 since I recieved it from the course  

## Motor Control
The motor control was done very similarly: a geared DC motor with an attached optical encoder was paired with the same DRV8874 H-bridge. The motor chosen did not also come with the wheel assembly like the initial design but it used the same (or at least visually identical) wheels. The main difference in the motor assembly then is that the motor is 6V instaed of 12V. In my [initial parts list] I mentioned how the reason I chose a 12V motor was because I was concerned that the size of the Segbot body would make it heavy enough that a more powerful motor would be needed. Since the body is redesigned to be much more minimalistic and lightweight, a 6V motor easily suffices. The specific motor chosen was the GM25-370 DC 6V geared motor.  

<p align="center">GM25-370 Motor</p>  

[Store Page](https://www.banggood.com/CHIHAI-MOTOR-GM25-370-DC-Gear-Motor-6V-100210300RPM-Encoder-Motor-p-1016183.html?ID=519629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)  
Cost: $27 for two motors + cost of two wheels  

Same H-bridge: DRV8874  
[Chip Datasheet](https://www.ti.com/lit/ds/symlink/drv8874.pdf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)  
[Texas Instruments Page](https://www.ti.com/product/DRV8874)  
Cost: $2.50 for two H-bridges  

An added feature to this design is a switch before the motor subassembly that will turn them on or off entirely. A potentiometer was also used in conjunction with each side of the motor subassembly, wired to the VREF pin of the H-bridge. Doing this allows me to regulate the maximum motor current. Other than some small changes because of these additions, my initial circuit design surrounding the H-bridge was fairly similar.  

## Sensors
A very similar Arduino module combining the accelerometer and gyroscope sensors was chosen. The main difference on this switch from using the MPU-6050 to now using the MPU-9250 is the the 9250 is a 9-axis sensor instead of a 6-axis sensor. The new module combines an accelerometer, gyroscope, and a magnometer which, similarly to upgrading the microcontroller, adds potential to do more advanced projects with the same hardware in the future. Otherwise, for this specific project the change doesn't affect performance on the Segbot.  

<p align="center">Accelerometer, Gyroscope, and Magnometer</p>  

[Chip Datasheet](https://invensense.tdk.com/wp-content/uploads/2015/02/PS-MPU-9250A-01-v1.1.pdf)  
[Store Page](https://www.amazon.com/HiLetgo-Gyroscope-Acceleration-Accelerator-Magnetometer/dp/B01I1J0Z7Y)  
Cost: $10  

## Battery
The power supply subsystem is probably the most complex change happening in the revised design (and I am not particularly skilled in designing power circuits). Prof. Block designed the PCB to be capable of being powered both by an AC outlet or a DC battery pack. On top of that, a 3V Lithium button cell battery (CR2032) was added to power a real-time clock that will be discussed in the next section. The primary power supply is run through a DC regulator (the TL1963A-33KTTR) to bring it to 5V, which is used to power the microcontroller. From there, the microcontroller regulates and distributes the power to the other parts of the system when they need either a 5V input or a 3.3V input.  

[TL1963A-33KTTR Datasheet](https://www.ti.com/lit/ds/symlink/tl1963a.pdf?HQS=dis-dk-null-digikeymode-dsf-pf-null-wwe&ts=1621389533941)  
[Store Page](https://www.digikey.com/en/products/detail/texas-instruments/TL1963A-33KTTR/1905593)  
Cost: $3

Since the AC power option is for working on a stationary board and the Segbot is mobile, I'm only focusing on the DC inputs. A battery pack of four AA batteries supplies 1.5V of current to the board's DC regulator. This input voltage is much smaller than my initial design's 11V battery, but we also need to consider that the motors require 6V instead of 12V and that my lack of experience with power circuits probably led me to overestimate. My initial DC/DC converter was still designed to bring the input 11V down to the needed 3.3V, and the DC regulator in this design is capable of brining down a voltage as high as 20V so it might still have been able to work with the old battery pack. Regardless, using a smaller battery pack is ideal because it allows for rechargable betteries and is ultimately cheaper.  

<p align="center">Main Power Supply</p>  

[Main Power Supply Store Page](https://www.amazon.com/gp/product/B07QV8GYV3/ref=ppx_yo_dt_b_asin_title_o05_s02?ie=UTF8&psc=1)  
Cost: $23  

[CR2032 Store Page](https://www.amazon.com/gp/product/B071D4DKTZ/ref=ppx_yo_dt_b_asin_title_o05_s00?ie=UTF8&psc=1)  
Cost: $6 for 10 (only 1 is needed)  

## Frame
Similar to the initial design, the frame is designed to be 3D printed for free on campus. More details can be found in the [CAD model](https://github.com/monk200/Segbot/tree/main/Frame/Reworked%20Frame%20Design) section.  

Cost: $0  

## Other Parts
As mentioned in the section on the new microcontroller, it has three quadrature encoders built in so the LS7366R is no longer needed. However, Prof. Block designed the PCB to have an external real-time clock (the BQ32000) connected to an external 32.768 kHz crystal oscillator. I don't have the specific part number of the cyrstal oscillator used but it does need to be one with two through-hole leads such as the ECS-.327-12.5-8X. The CR2032 battery directly powers the BQ32000.  

[BQ32000 Datasheet](https://www.ti.com/lit/ds/symlink/bq32000.pdf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)  
[BQ32000 Store Page](https://www.mouser.com/ProductDetail/Texas-Instruments/BQ32000DR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)  
Cost: $2  

[ECS-.327-12.5-8X Datasheet](https://ecsxtal.com/store/pdf/ECS-3x8X%202x6X%201X5X.pdf)  
[ECS-.327-12.5-8X Store Page](https://www.digikey.com/en/products/detail/ecs-inc/ECS-327-12-5-8X/827614)  
Cost: $0.30

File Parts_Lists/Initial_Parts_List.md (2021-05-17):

# Parts List for the Initial Design
The first portion of this project initially allowed for the flexibility to design a Segbot of any size, but because I was intending to build it eventually I went in trying to pick cost-effective hobbyist parts. Below are details on the process of selecting each part.   

## Microcontroller
The original design was intended to use the MSP430G2553 microcontroller (on the TI development board) because it was used earlier in the course for homework projects and tinkering so it was a part I already owned and was familiar with. The MSP430 controller is a low-power, high-performance, 16-bit general purpose controller. This particular MSP430 chip has 512 bytes SRAM, 24 I/O pins, 8 ADC channels with 10 bit resoultion, and two 16-bit timers. Below is a simple pinout of the launchpad board used:  
<p align="center">MSP430 Pinout</p>  

[Texas Instruments Page](https://www.ti.com/product/MSP430G2553#product-details##params)  
[Chip Datasheet](https://www.ti.com/lit/ds/symlink/msp430g2553.pdf)  
[Launchpad Datasheet](https://www.ti.com/lit/ug/slau772a/slau772a.pdf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)  
[Store page](https://www.digikey.com/en/products/detail/texas-instruments/MSP-EXP430G2ET/9608004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)  

Cost: $12 on digikey.com, $0 since I recieved it from the course  

## Motor Control
This was the first time I had experience choosing a motor and battery to begin creating a project (as opposed to having a starting kit). From the start, I knew I was searching for a 6-12V DC hobby motor because that was the kind of motors I've used before for robot car projects. Choosing a DC motor over an AC motor here is a no-brainer because AC motors need to be driven by AC current and tend to be used in stationary, high-load situations. Generally on my other robot cars, a 6V motor was sufficient but because of the added weight of the Segbot body it might be necessary to increase the voltage. Further calculations for this can be seen below, using estimated parameters from the rest of the Segbot build. Exploring other robot car kits and projects also led me to belive that the exact type of motor needed should be a micro gear reduction motor. Further research into why showed that often times DC motors rotate significantly faster than necessary for most applications and difficult to control, so adding the gearbox reduces the speed to a reasonable level and increases the motor's torque. Another consideration when choosing the motor is its compatibility with an optical encoder and wheels. Installing an optical encoder to a motor adds a more intensive task with notable room for error so immediately I took the luxury of not considering any motors that did not come pre-installed with an optical encoder. While browsing the remaining options, it was clear that I could also take the luxury of choosing a motor that also came with its own wheel. This continued to simplify my work because I didn't need to match up shaft sizes or be concerned about the width of the motor. Ultimately, the approach of getting the whole subassmbly together did make the final choice cheaper than the alternatives. The chosen motor subassembly was the Machifit 25GA370 DC 12V Micro Gear Reduction Motor and its details can be found below.  

<p align="center">
Motor Subassembly
Encoder Pinout
</p>  

[Store Page](https://www.banggood.com/Machifit-25GA370-DC-12V-Micro-Gear-Reduction-Encoder-Motor-with-Mounting-Bracket-and-Wheel-p-1532242.html?ID=6157425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)  
Cost: $40 for two motors  

An H-bridge is essential to be able to control the direction of the motor. The stall current of the chosen motor corresponds to the maximum continuous current the H-bridge needs to produce. The chosen motor's stall current is 1.8A so the H-bridge needs to have a peak output current that is sufficient. Searching [TI's selection of motor drivers](https://www.ti.com/motor-drivers/brushed-dc-bdc-drivers/overview.html) led to many seemingly suitable options. Because most students in the course were struggling selecting an H-bridge they could be confident would work, Prof. Block suggested a few options that he was familiar with and knew would work for different Segbot sizes. In my hobby-sized Segbot, he recommended the DRV8874.

[Chip Datasheet](https://www.ti.com/lit/ds/symlink/drv8874.pdf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)  
[Texas Instruments Page](https://www.ti.com/product/DRV8874)  
Cost: $2.50 for two H-bridges  

## Sensors
Aside from the motor encoders, the only other sensors required for the balancing control are an accelerometer and gyroscope. This part was actually extremely easy to find because there is a popular Arduino module that combines both sensors, and since it's made for the Arduino it will also easily be able to be used with the MSP430. The module chosen was the MPU-6050:  

<p align="center">Accelerometer and Gyroscope</p>  

[Chip Datasheet](http://myosuploads3.banggood.com/products/20190227/20190227200210MPU-6050InvenSense.pdf)  
[Store page](https://www.banggood.com/Geekcreit-6DOF-MPU-6050-3-Axis-Gyro-With-Accelerometer-Sensor-Module-p-80862.html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)  
Cost: $4  

## Battery
Again since I didn't have much experience determining what kind of battery a system needed, I was guided by Prof. Block to choose a lithium ion battery. He advised that it should have 2-3 cells and be rated for 1500-2500 mAh. The LiPo battery is ideal because it is lightweight and rechargable, even though it is important to be very careful to not short the leads. The battery I ended up choosing was specifically for hobby applications and its details are shown below:  

[Store page](https://www.amazon.com/Zeee-3000mAh-Connector-Airplane-Helicopter/dp/B07VLR5ZW9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)  
Cost: $40 for two, though only one is needed  

Lastly, a DC-DC converter would be needed to scale the battery power down to power the MSP430. Since the battery chosen provides 11.1V and the MSP430 needs a 3.3V input, the chosen converter needs to fit that range. It was easy enough to find the OKI-78SR, with up to a 36V input and a 3.3V output:  

[Store page](https://www.digikey.com/en/products/detail/murata-power-solutions-inc/OKI-78SR-3.3-1.5-W36-C/2259780)  
[Chip Datasheet](https://www.murata.com/products/productdata/8807037992990/oki-78sr.pdf?1583754815000)  
Cost: $4.50  

## Frame
Since I had free access to a 3D printer while in school, the body of the Segbot was planned to be 3D printed. This firstly creates an opportunity to work on my CAD skills and learn to use a 3D printer, but also allows the flexibility to create a custom-shaped body. More details can be found in the [CAD model]() section.  

Cost: $0

## Other Parts
A few parts needed for the assembly were provided by Prof. Block without detailed explanation. The first is the LS7366R Quadrature Counter, which is used to communicate with the MSP430's SPI. The other part is a crystal oscillator whose pinout was provided but specific part number was not. The connections between these parts and the controller's SPI peripheral can be seen on the last page of [this link](http://coecsl.ece.illinois.edu/ge423/LS7366CodeHandout.pdf). The first three pages contain the code needed to initialize the SPI on the microcontroller.  

[LS7366R Datasheet](https://lsicsi.com/datasheets/LS7366R.pdf)  

## Sources
https://www.powerelectric.com/motor-resources/motors101/what-are-dc-motors-usually-gear-motors  
https://www.engineersgarage.com/tech-articles/choosing-motor-for-robots/  
https://rogershobbycenter.com/lipoguide

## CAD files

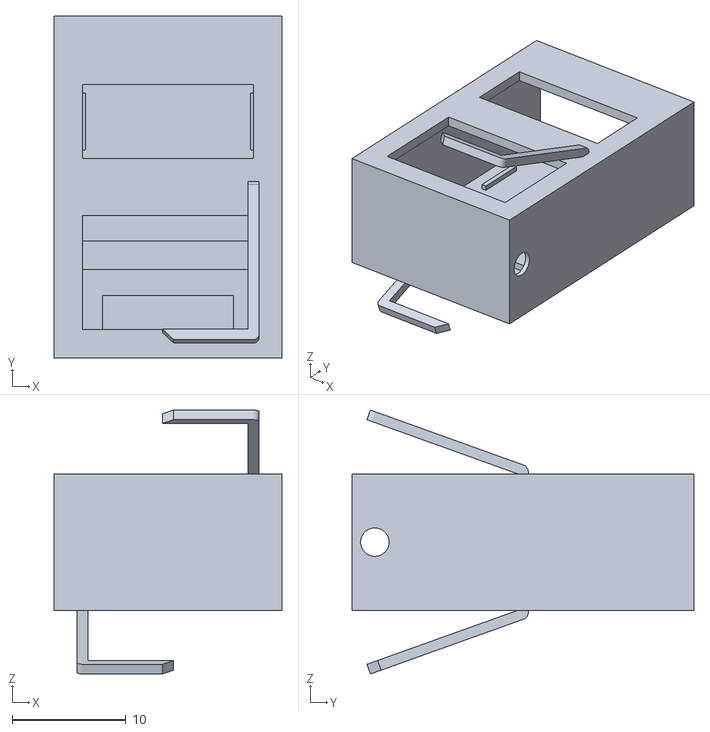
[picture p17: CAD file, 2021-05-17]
Frame/Initial Frame Design/segbot_frame.stl
20.0 x 30.0 x 23.2

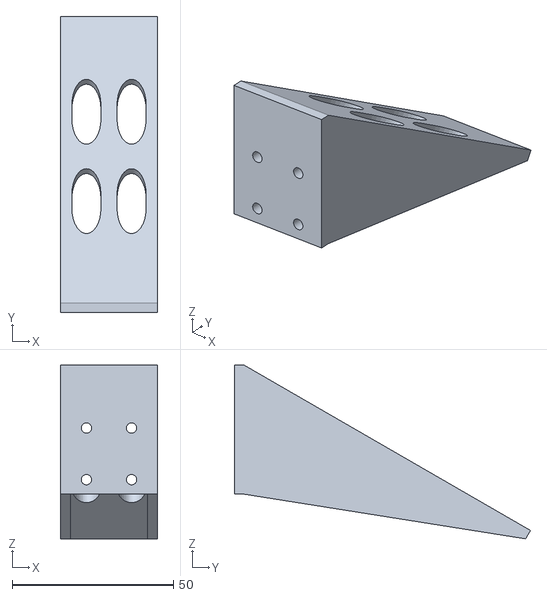
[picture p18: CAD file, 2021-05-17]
Frame/Reworked Frame Design/support_d9.STL
30.0 x 91.8 x 53.8

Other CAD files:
Frame/Reworked Frame Design/segbot_frame.dwg
Frame/Initial Frame Design/segbot_frame.dwg

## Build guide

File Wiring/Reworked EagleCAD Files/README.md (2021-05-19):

# PCB for Reworked Design
Prof. Block used EagleCAD to design the circuit board for the reworked design. The circuit schematic can be seen to connect each part in the way my [reworked wiring diagram](https://github.com/monk200/Segbot/blob/main/Wiring/Initial%20Design%20Wiring%20Diagram.png) does, but my diagram only has the essential peripherials to make the Segbot work. The board was fabricated at https://www.4pcb.com/ and my professor uses its [free file checker](https://www.4pcb.com/free-pcb-file-check/index.html).  

## Wiring Considerations
This board design is significantly more complex because the board was designed with the intent of using it for any number of personal projects. My initial design minimized complexity because I was focusing on the project at hand and I am less experienced than my Professor. When looking through his design, he added a switch to power the motor subassembly on and off and a potentiometer for each motor connected to the H-bridge's VREF pin. This allows the user to regulate the maximum motor current. Other major changes from my design include that Prof. Block's design needs to have an external real-time clock but does not need external quadrature encoders. The most complex difference between my design and Prof. Block's design is the power system. Prof. Block designed this PCB to be able to be powered by an AC outlet or by a DC battery pack. Since the Segbot is a mobile project, I only focused on deconstructing the DC power system.  

## EagleCAD Design
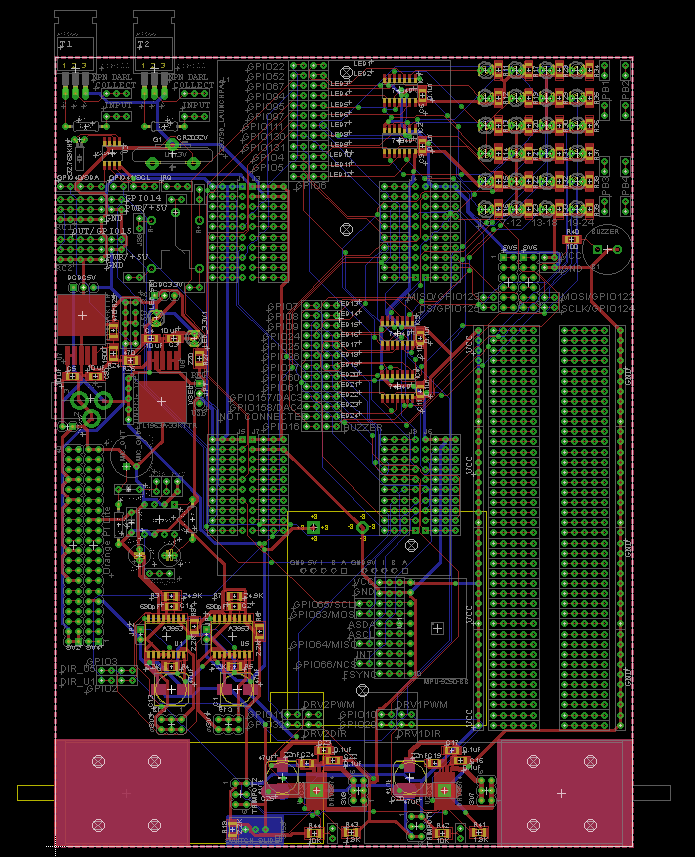
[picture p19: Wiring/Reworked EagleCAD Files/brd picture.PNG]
BRD
  

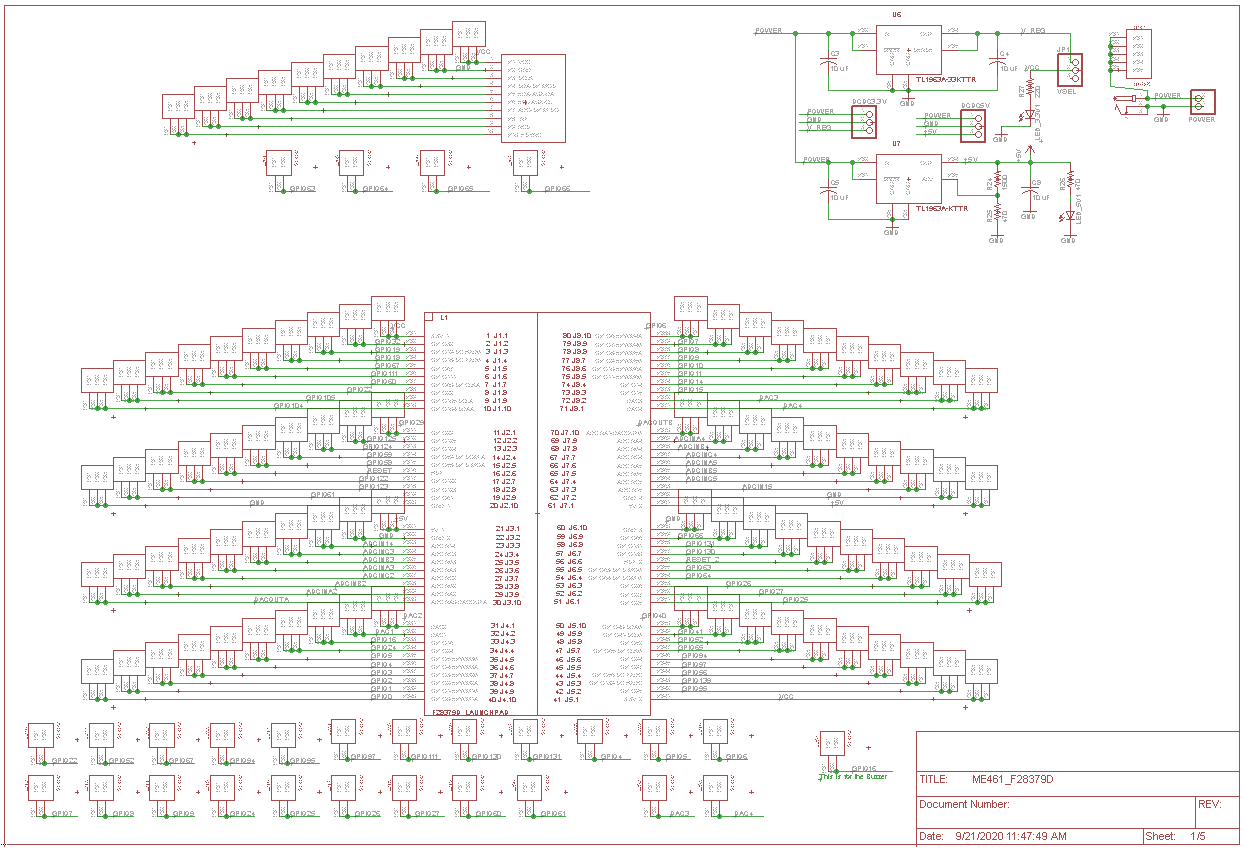
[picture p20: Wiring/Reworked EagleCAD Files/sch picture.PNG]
  

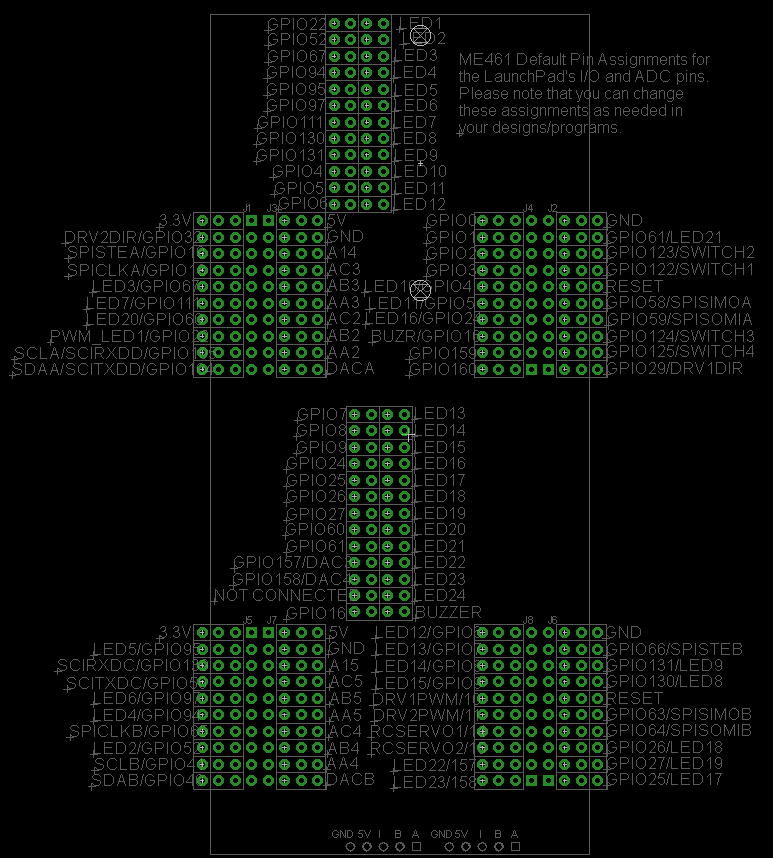
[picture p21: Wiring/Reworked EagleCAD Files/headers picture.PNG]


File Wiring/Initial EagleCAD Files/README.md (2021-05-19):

# PCB for Initial Design
EagleCAD was used to design the circuit board for the initial design. The circuit schematic can be seen to very closely resemble the [initial wiring diagram](https://github.com/monk200/Segbot/blob/main/Wiring/Initial%20Design%20Wiring%20Diagram.png). The board was intened to be fabricated at https://www.4pcb.com/ because students get a discount that their boards only cost $33 and they have their own [free file checker](https://www.4pcb.com/free-pcb-file-check/index.html).  

## Wiring Considerations
I tethered the AD0 pin on the MPU-6050 to ground because it is used to toggle between two slave addresses, which is unneccesary in this case. By tethering it to ground, the slave address is set to 0x68 and one less pin on the MSP-430 needs to be occupied. I also connected PMODE on both DRV8874 chips to ground to select the control mode that takes an enable input and a phase. The capacitors and resistors connected directly to the DRV8874 chips are based on the diagram from [page 9 of the datasheet](https://www.ti.com/lit/ds/symlink/drv8874.pdf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). Lastly, since the MPU-6050 is already using UCB for its clock and reading data, the LS73366R chips are using UCA instead of leaving UCA for connecting to a terminal emulator. This is slightly inconvenient for programming and debugging purposees but is a necesssary sacrifice to connect the required circuitry.  

## Custom Parts
The only custom part that I needed to create was the MPU-6050 ([MPU6050_MODULE in SE423EagleLibrary.lbr](https://github.com/monk200/Segbot/blob/main/Wiring/Initial%20EagleCAD%20Files/SE423EagleLibrary.lbr)). The module chosen didn't list the exact information on the pin spacing so some assumptions were made that since it is technically an Arduino module, the pins would be spaced the same distance apart. Other than that, the circuit design was fairly simple to work through.  

## 4PCB File Check
Running my design through the free file checker produced no major issues and it automatically fixed a recurring line width error I made. The specific error message output was "Insufficient Silkscreen Line Width (1543 violations)," and, as I noted, the file checker automatically fixed the error.  

## EagleCAD Design
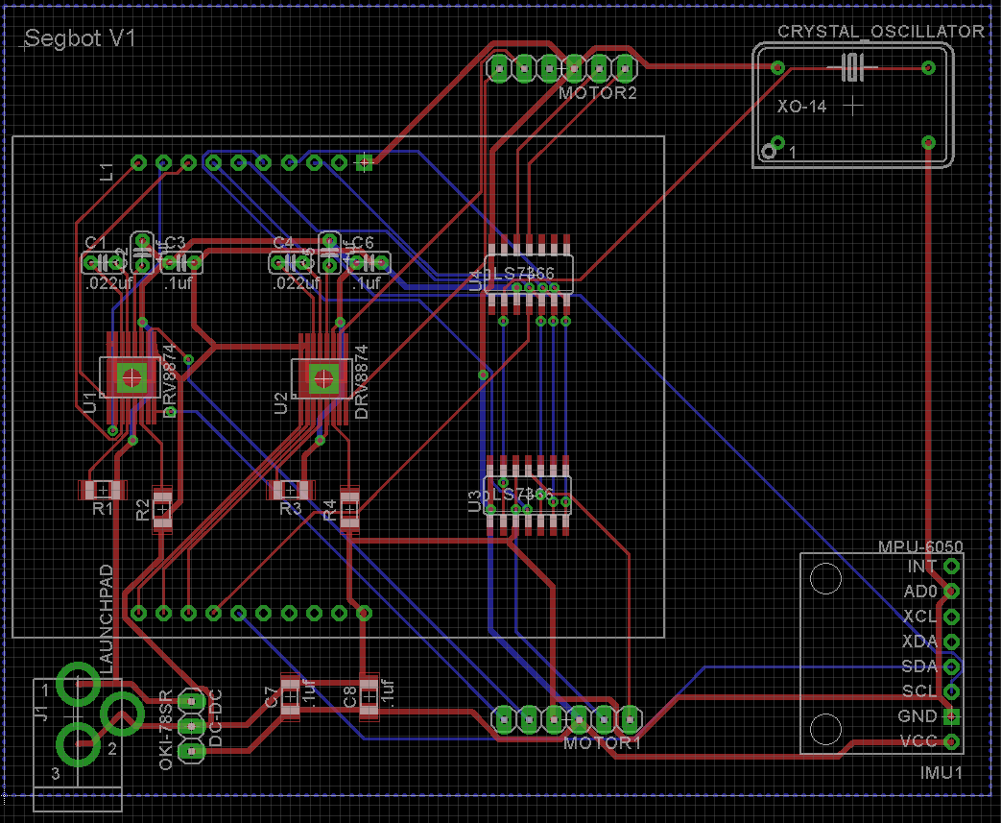
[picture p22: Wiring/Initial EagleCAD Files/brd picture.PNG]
BRD
  

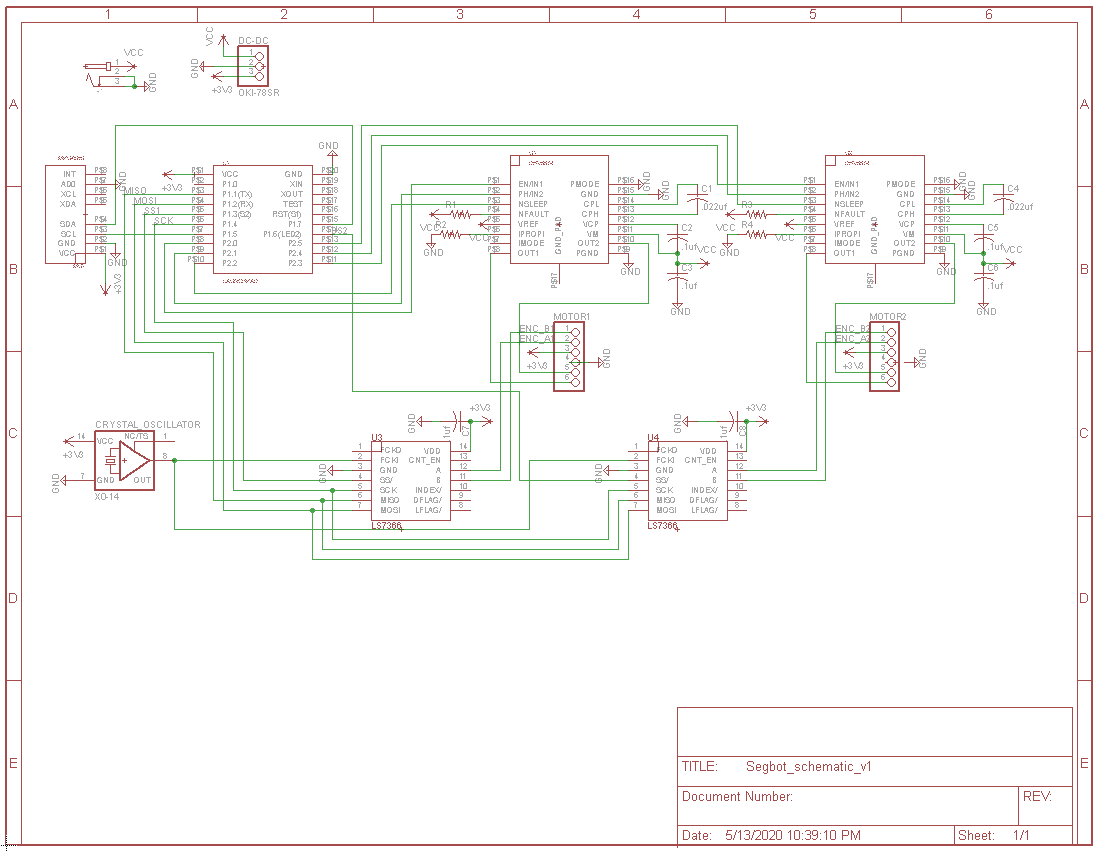
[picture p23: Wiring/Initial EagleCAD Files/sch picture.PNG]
SCH


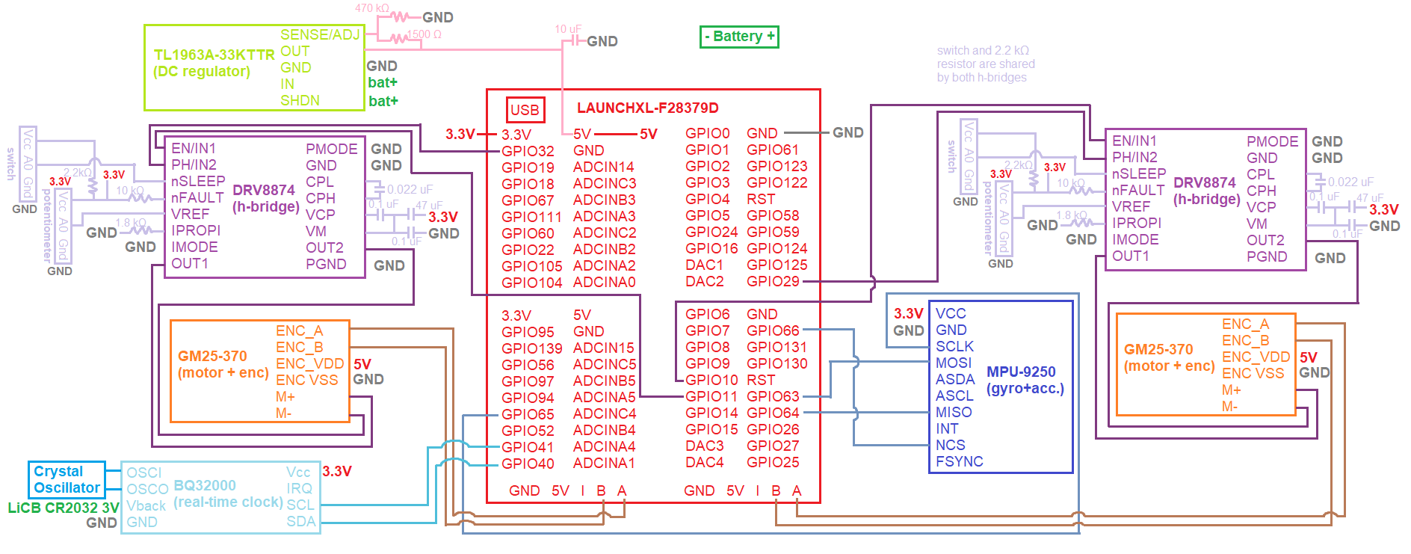
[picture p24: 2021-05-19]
Wiring/Reworked Wiring Diagram.png

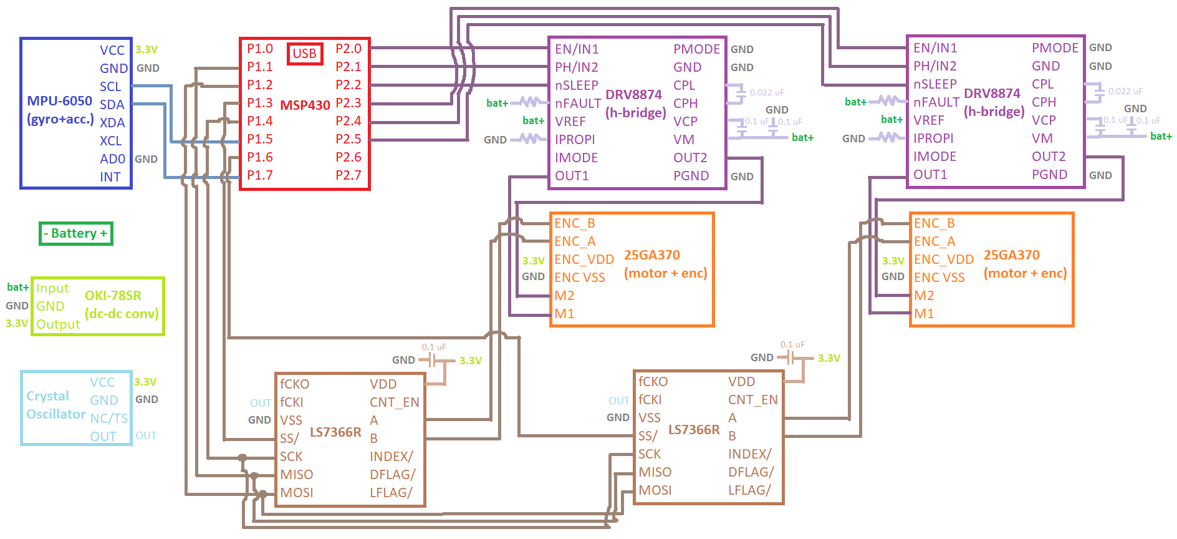
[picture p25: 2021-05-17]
Wiring/Initial Design Wiring Diagram.png

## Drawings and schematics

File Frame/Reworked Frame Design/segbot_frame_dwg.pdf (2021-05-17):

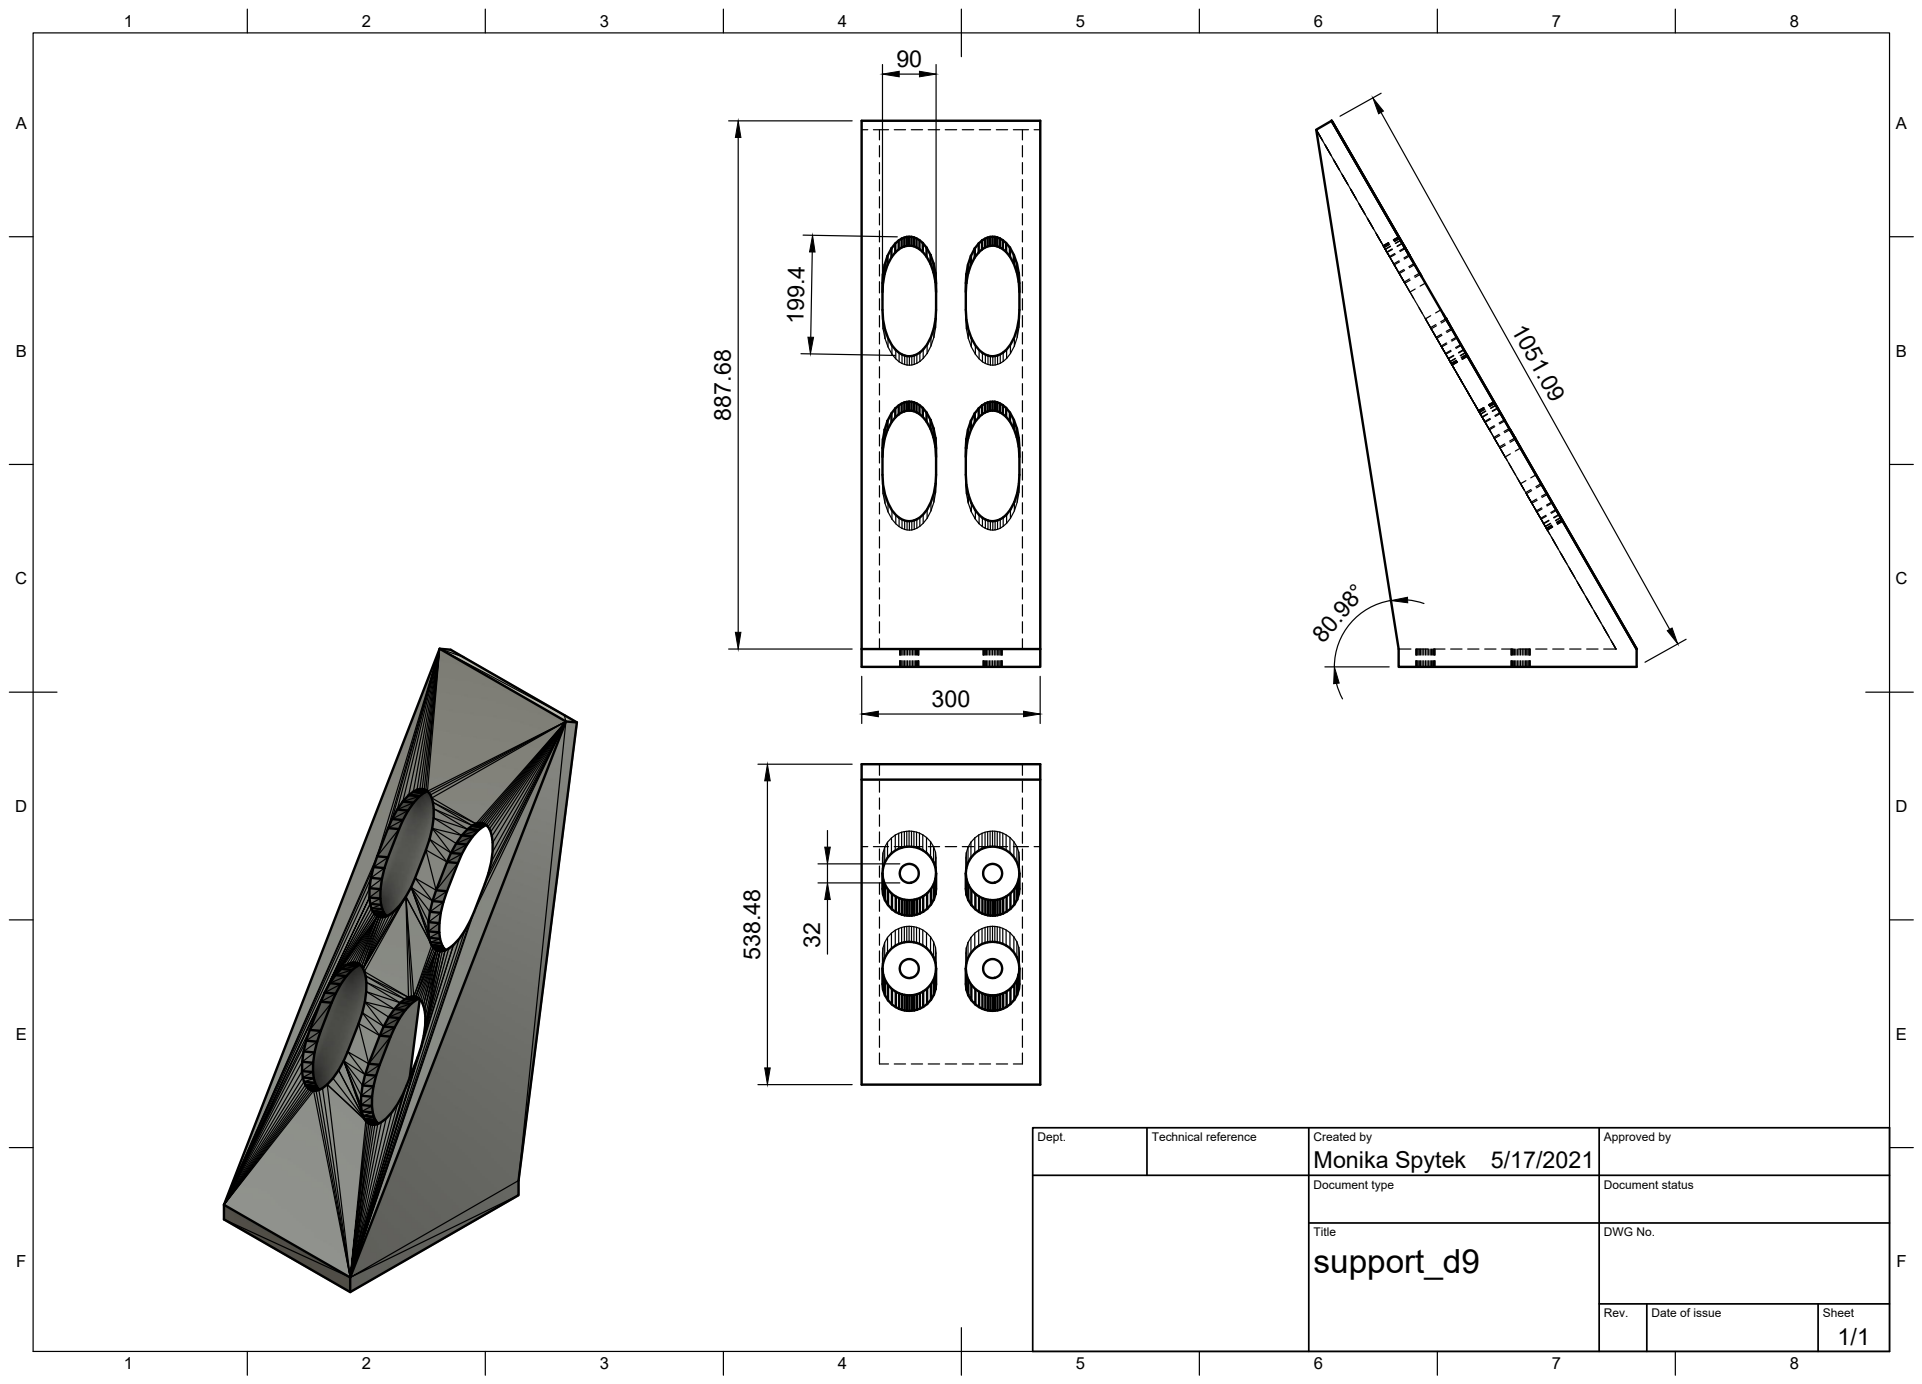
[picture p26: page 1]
Title; DWG No.; Rev.; Date of issue; Sheet; Monika Spytek 199.4

Dept. | Technical reference | Created by 5/17/2021 | Approved by

Document type | Document status

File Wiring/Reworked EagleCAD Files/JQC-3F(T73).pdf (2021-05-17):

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

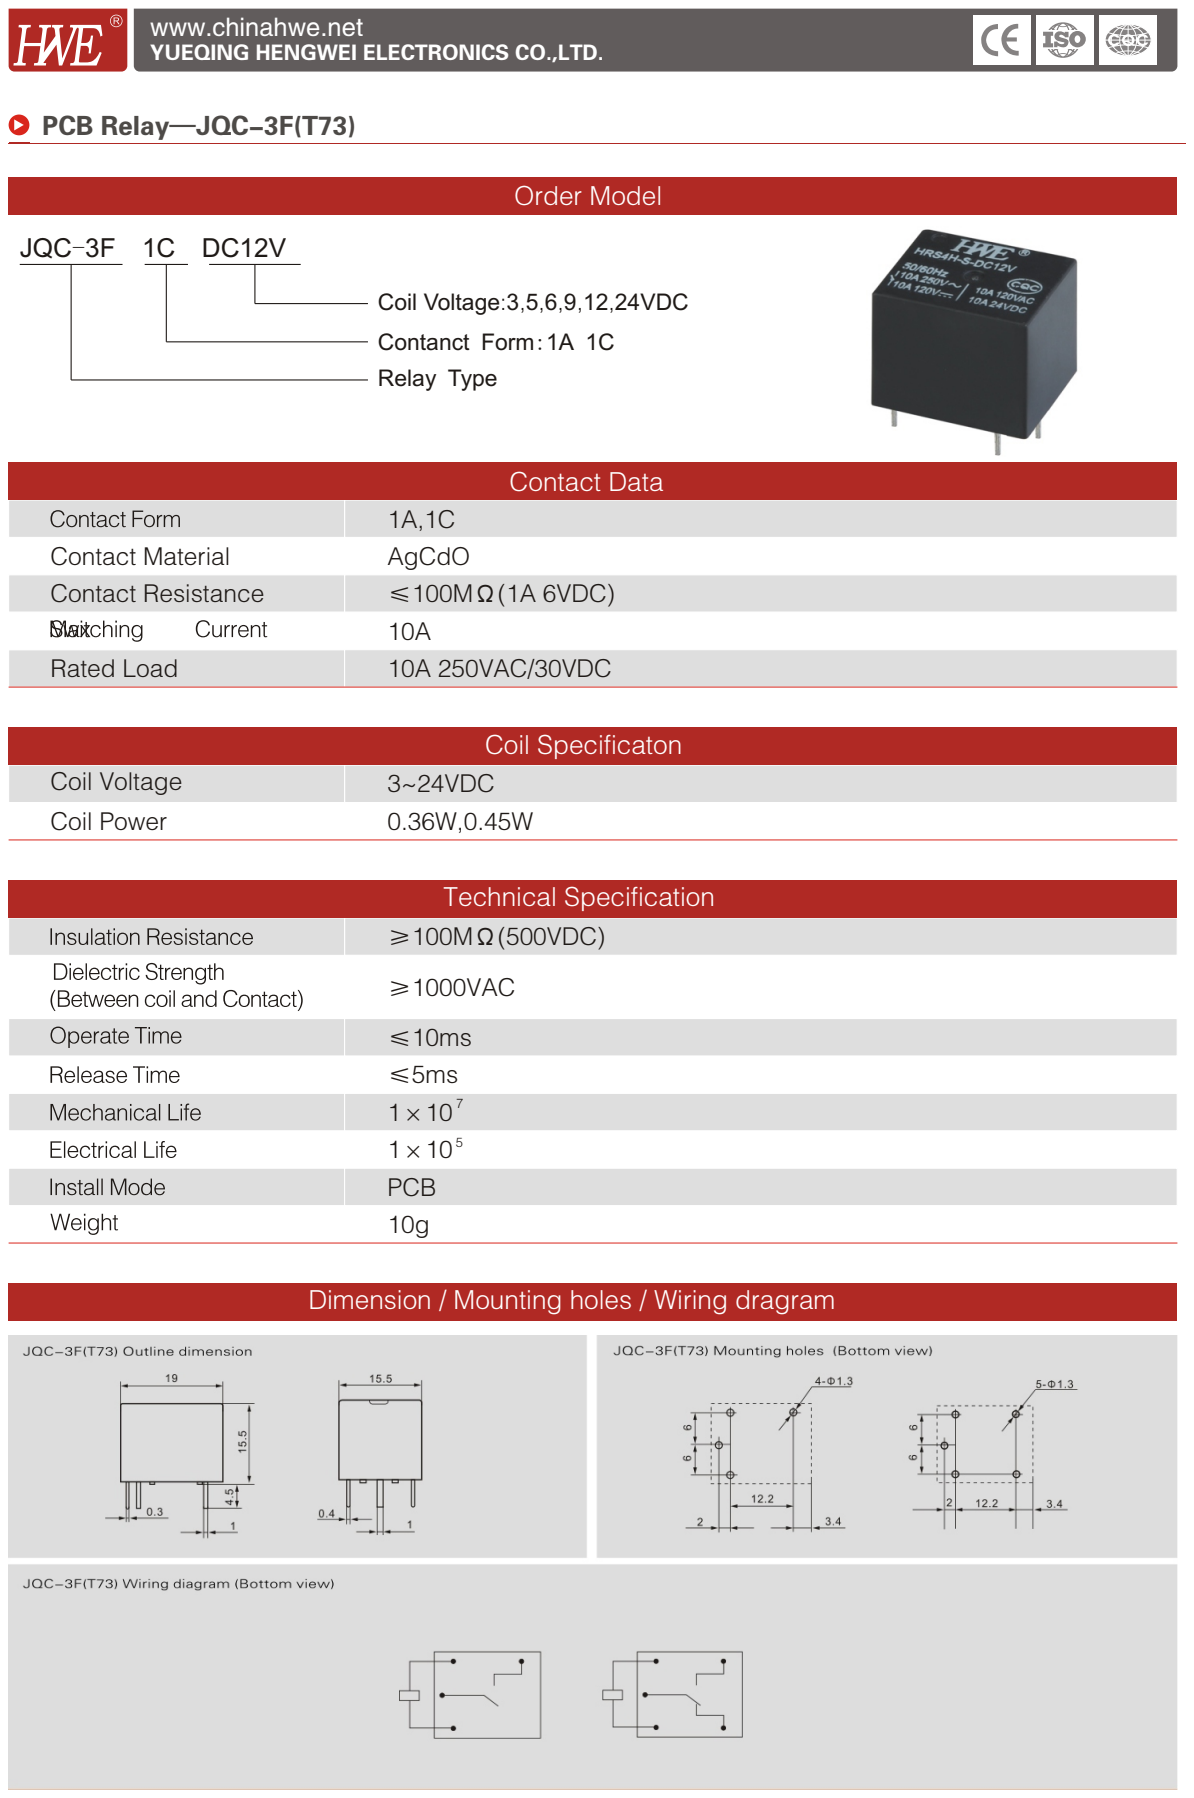
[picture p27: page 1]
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

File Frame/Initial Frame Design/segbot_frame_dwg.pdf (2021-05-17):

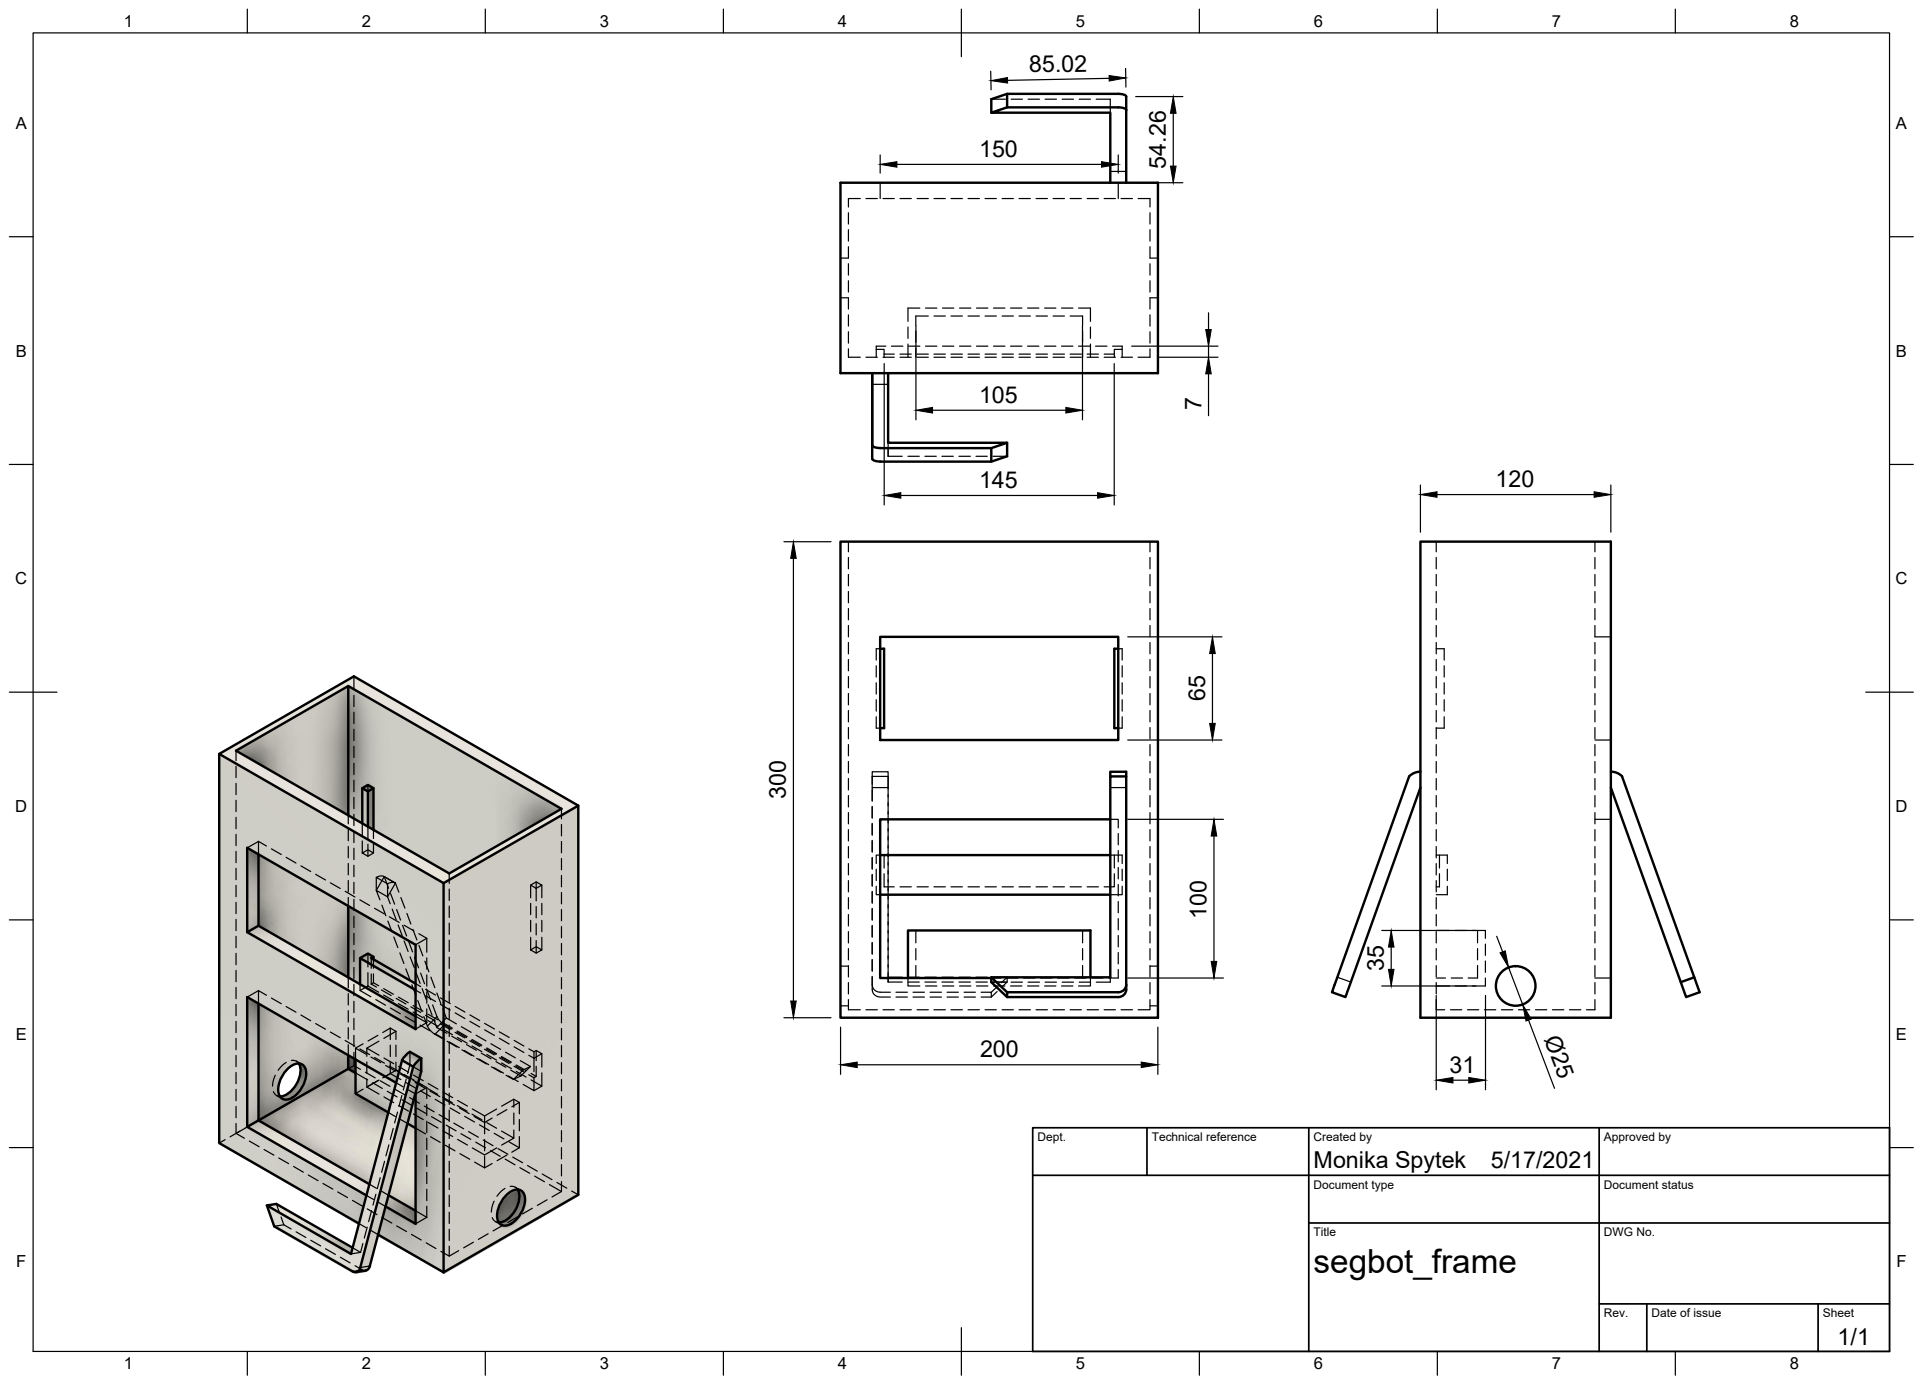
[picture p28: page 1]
Title; DWG No.; Rev.; Date of issue; Sheet; Monika Spytek 54.26

Dept. | Technical reference | Created by 5/17/2021 | Approved by

Document type | Document status

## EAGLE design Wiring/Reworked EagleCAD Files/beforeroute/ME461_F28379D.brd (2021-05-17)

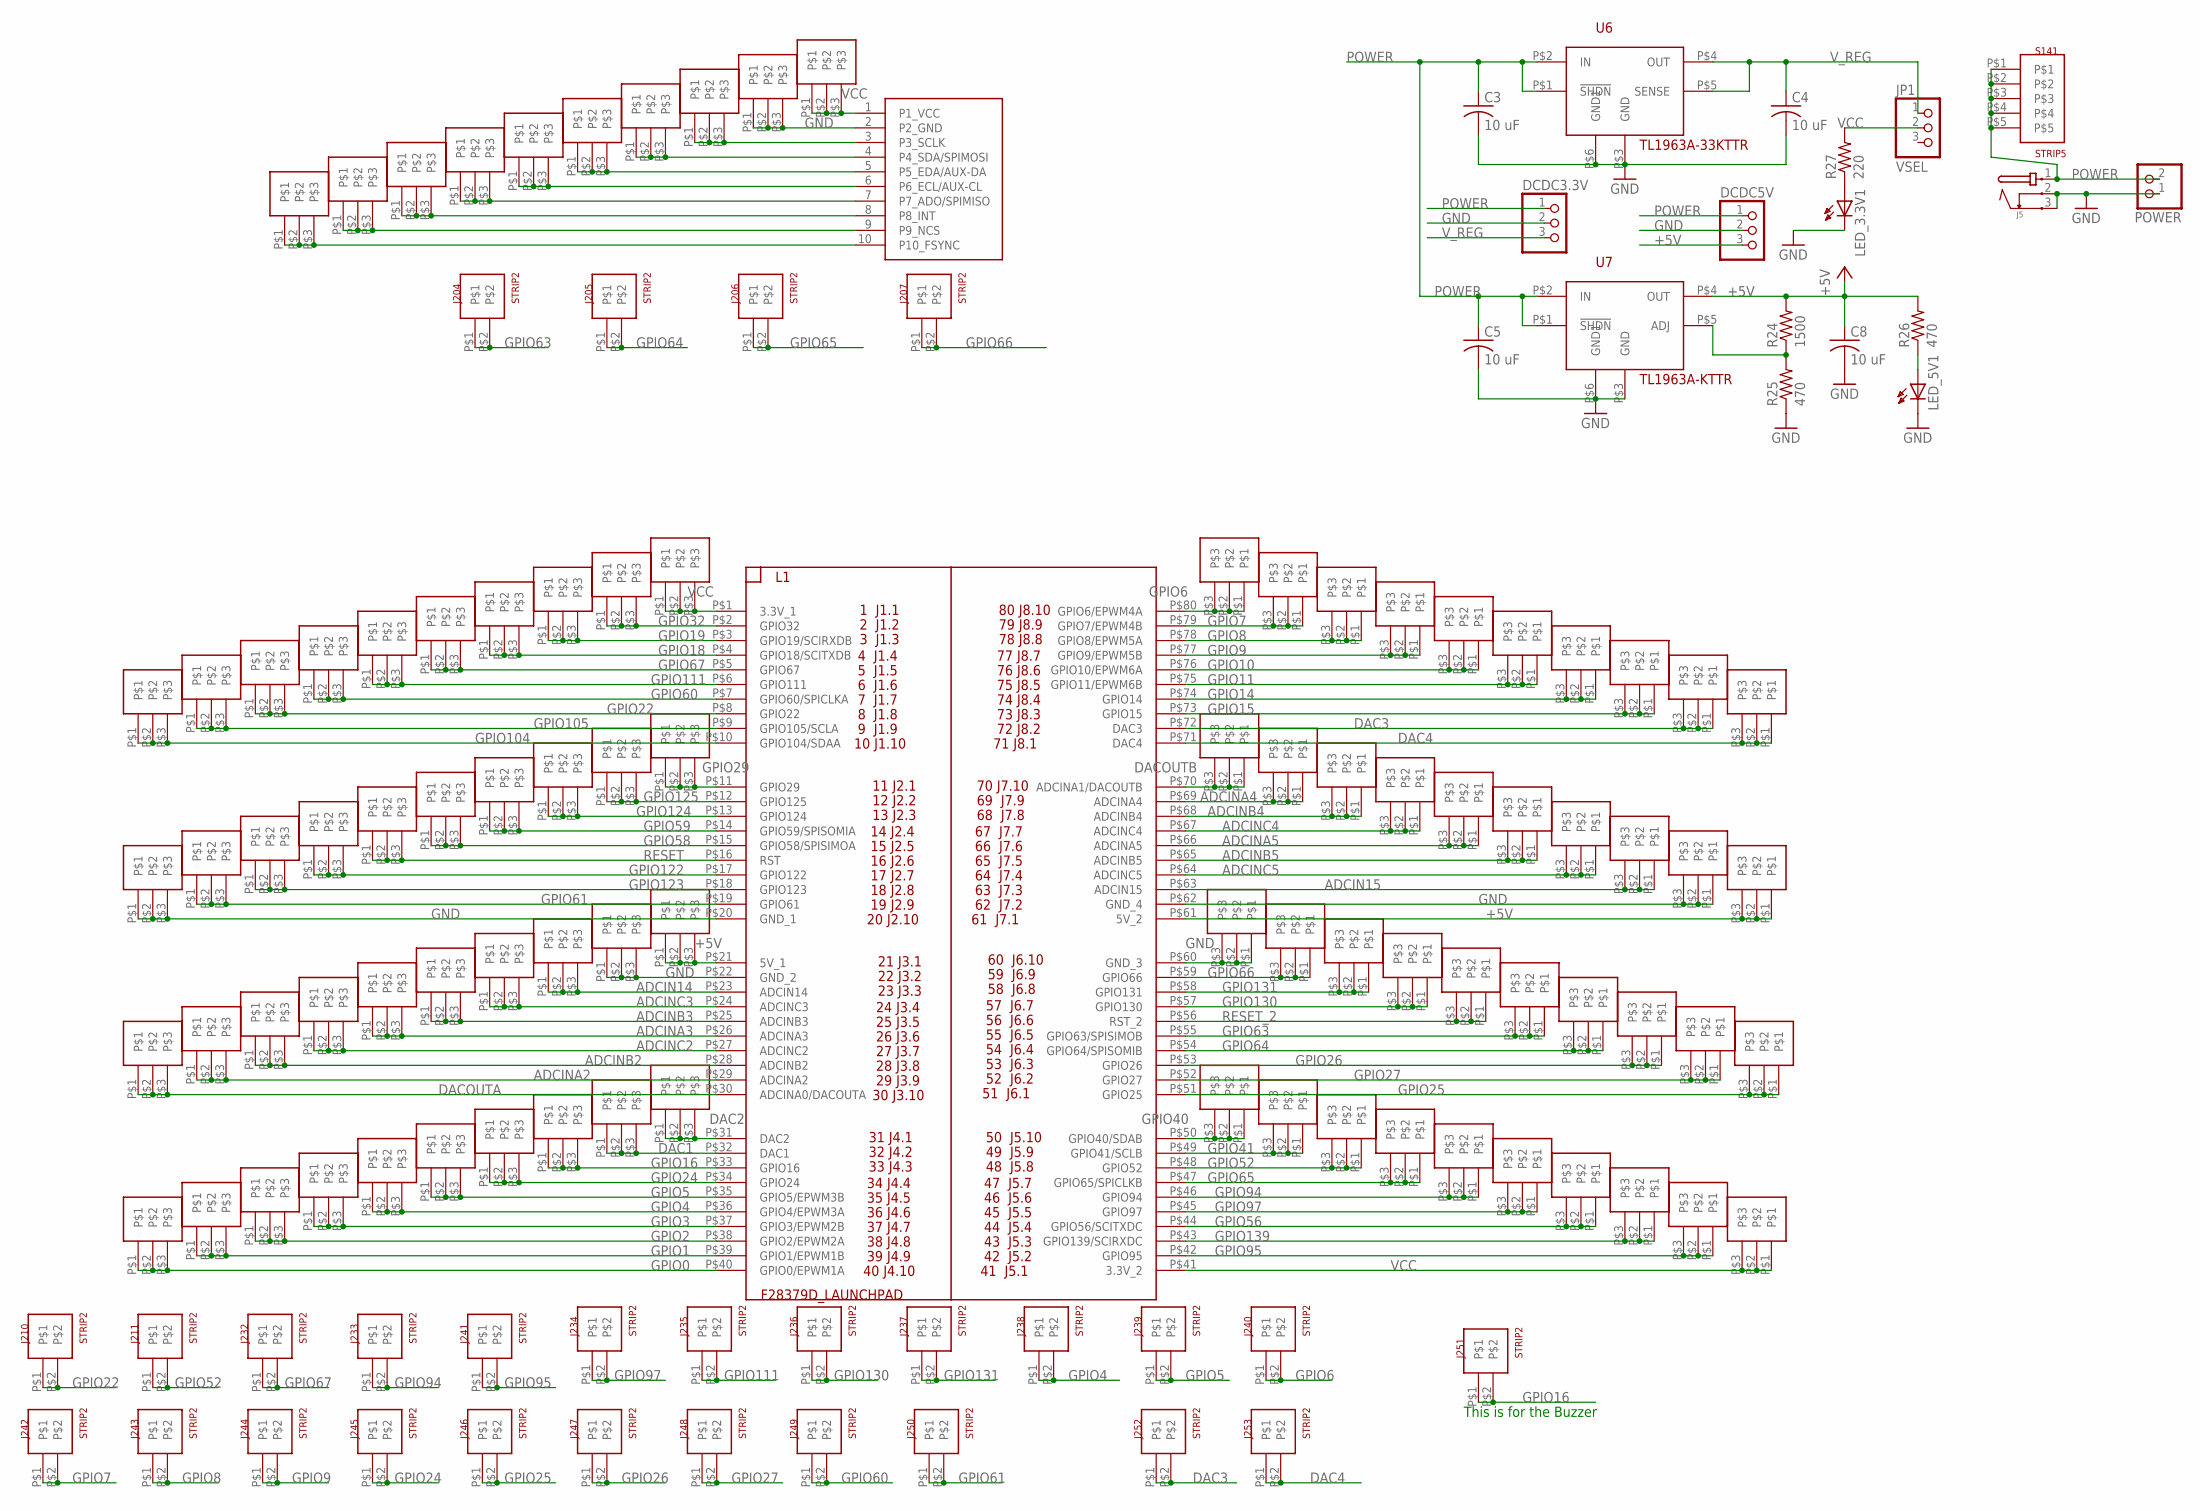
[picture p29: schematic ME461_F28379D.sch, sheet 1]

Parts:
C3, C4, C5, C8: 10 uF; C1206
DCDC3.3V, DCDC5V: PINHD-1X3; 1X03
J5: JACK-PMS
J10, J14, J15, J16, J17, J18, J19, J20, J21, J28, J29, J30, J31, J32, J33, J98, J99, J100, J101, J102, J103, J104, J105, J106, J107, J108, J109, J110, J111, J112, J113, J114, J115, J116, J117, J118, J119, J120, J121, J122, J123, J124, J125, J126, J127, J128, J129, J130, J131, J132, J133, J134, J135, J136, J137, J138, J139, J140, J141, J142, J143, J144, J145, J146, J147, J148, J149, J150, J151, J152, J153, J154, J155, J156, J157, J158, J159, J160, J161, J162, J163, J164, J165, J166, J167, J168, J169, J170, J176, J177: STRIP3
J204, J205, J206, J207, J210, J211, J232, J233, J234, J235, J236, J237, J238, J239, J240, J241, J242, J243, J244, J245, J246, J247, J248, J249, J250, J251, J252, J253: STRIP2
JP1: VSEL; 1X03
L1: F28379D_LAUNCHPAD
LED_3.3V1, LED_5V1: LED3MM
POWER: PINHD-1X2; 1X02
R24: 1500; M1206
R25, R26: 470; M1206
R27: 220; M1206
S141: STRIP5
U6: TL1963A-33KTTR; TL1963AKTTR
U7: TL1963A-KTTR; TL1963AKTTR
U$1: MPU-9250-BB

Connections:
+5V: C8.1, DCDC5V.3, J103.P$1, J103.P$2, J103.P$3, J152.P$1, J152.P$2, J152.P$3, L1.P$21 (5V_1), L1.P$61 (5V_2), R24.2, R26.2, U7.P$4 (OUT); also elsewhere on the board
ADCIN14: J105.P$1, J105.P$2, J105.P$3, L1.P$23 (ADCIN14)
ADCIN15: J150.P$1, J150.P$2, J150.P$3, L1.P$63 (ADCIN15)
ADCINA2: J111.P$1, J111.P$2, J111.P$3, L1.P$29 (ADCINA2)
ADCINA3: J108.P$1, J108.P$2, J108.P$3, L1.P$26 (ADCINA3)
ADCINA4: J144.P$1, J144.P$2, J144.P$3, L1.P$69 (ADCINA4)
ADCINA5: J147.P$1, J147.P$2, J147.P$3, L1.P$66 (ADCINA5)
ADCINB2: J110.P$1, J110.P$2, J110.P$3, L1.P$28 (ADCINB2)
ADCINB3: J107.P$1, J107.P$2, J107.P$3, L1.P$25 (ADCINB3)
ADCINB4: J145.P$1, J145.P$2, J145.P$3, L1.P$68 (ADCINB4)
ADCINB5: J148.P$1, J148.P$2, J148.P$3, L1.P$65 (ADCINB5)
ADCINC2: J109.P$1, J109.P$2, J109.P$3, L1.P$27 (ADCINC2)
ADCINC3: J106.P$1, J106.P$2, J106.P$3, L1.P$24 (ADCINC3)
ADCINC4: J146.P$1, J146.P$2, J146.P$3, L1.P$67 (ADCINC4)
ADCINC5: J149.P$1, J149.P$2, J149.P$3, L1.P$64 (ADCINC5)
DAC1: J114.P$1, J114.P$2, J114.P$3, L1.P$32 (DAC1)
DAC2: J113.P$1, J113.P$2, J113.P$3, L1.P$31 (DAC2)
DAC3: J141.P$1, J141.P$2, J141.P$3, J252.P$1, J252.P$2, L1.P$72 (DAC3)
DAC4: J142.P$1, J142.P$2, J142.P$3, J253.P$1, J253.P$2, L1.P$71 (DAC4)
DACOUTA: J112.P$1, J112.P$2, J112.P$3, L1.P$30 (ADCINA0/DACOUTA)
DACOUTB: J143.P$1, J143.P$2, J143.P$3, L1.P$70 (ADCINA1/DACOUTB)
GND: C3.2, C4.2, C5.2, C8.2, DCDC3.3V.2, DCDC5V.2, J5.2, J5.3, J102.P$1, J102.P$2, J102.P$3, J104.P$1, J104.P$2, J104.P$3, J124.P$1, J124.P$2, J124.P$3, J151.P$1, J151.P$2, J151.P$3, J153.P$1, J153.P$2, J153.P$3, L1.P$20 (GND_1), L1.P$22 (GND_2), L1.P$60 (GND_3), L1.P$62 (GND_4), LED_3.3V1.K (C), LED_5V1.K (C), POWER.1, R25.1, U6.P$3 (GND), U6.P$6 (GND1), U7.P$3 (GND), U7.P$6 (GND1), U$1.2 (P2_GND); also elsewhere on the board
GPIO0: J122.P$1, J122.P$2, J122.P$3, L1.P$40 (GPIO0/EPWM1A)
GPIO1: J121.P$1, J121.P$2, J121.P$3, L1.P$39 (GPIO1/EPWM1B)
GPIO2: J120.P$1, J120.P$2, J120.P$3, L1.P$38 (GPIO2/EPWM2A); also elsewhere on the board
GPIO3: J119.P$1, J119.P$2, J119.P$3, L1.P$37 (GPIO3/EPWM2B); also elsewhere on the board
GPIO4: J118.P$1, J118.P$2, J118.P$3, J238.P$1, J238.P$2, L1.P$36 (GPIO4/EPWM3A)
GPIO5: J117.P$1, J117.P$2, J117.P$3, J239.P$1, J239.P$2, L1.P$35 (GPIO5/EPWM3B)
GPIO6: J133.P$1, J133.P$2, J133.P$3, J240.P$1, J240.P$2, L1.P$80 (GPIO6/EPWM4A)
GPIO7: J134.P$1, J134.P$2, J134.P$3, J242.P$1, J242.P$2, L1.P$79 (GPIO7/EPWM4B)
GPIO8: J135.P$1, J135.P$2, J135.P$3, J243.P$1, J243.P$2, L1.P$78 (GPIO8/EPWM5A)
GPIO9: J136.P$1, J136.P$2, J136.P$3, J244.P$1, J244.P$2, L1.P$77 (GPIO9/EPWM5B)
GPIO10: J137.P$1, J137.P$2, J137.P$3, L1.P$76 (GPIO10/EPWM6A); also elsewhere on the board
GPIO11: J138.P$1, J138.P$2, J138.P$3, L1.P$75 (GPIO11/EPWM6B); also elsewhere on the board
GPIO14: J139.P$1, J139.P$2, J139.P$3, L1.P$74 (GPIO14); also elsewhere on the board
GPIO15: J140.P$1, J140.P$2, J140.P$3, L1.P$73 (GPIO15); also elsewhere on the board
GPIO16: J115.P$1, J115.P$2, J115.P$3, J251.P$1, J251.P$2, L1.P$33 (GPIO16)
GPIO18: J16.P$1, J16.P$2, J16.P$3, L1.P$4 (GPIO18/SCITXDB)
GPIO19: J15.P$1, J15.P$2, J15.P$3, L1.P$3 (GPIO19/SCIRXDB)
GPIO22: J20.P$1, J20.P$2, J20.P$3, J210.P$1, J210.P$2, L1.P$8 (GPIO22)
GPIO24: J116.P$1, J116.P$2, J116.P$3, J245.P$1, J245.P$2, L1.P$34 (GPIO24)
GPIO25: J162.P$1, J162.P$2, J162.P$3, J246.P$1, J246.P$2, L1.P$51 (GPIO25)
GPIO26: J160.P$1, J160.P$2, J160.P$3, J247.P$1, J247.P$2, L1.P$53 (GPIO26)
GPIO27: J161.P$1, J161.P$2, J161.P$3, J248.P$1, J248.P$2, L1.P$52 (GPIO27)
GPIO29: J29.P$1, J29.P$2, J29.P$3, L1.P$11 (GPIO29); also elsewhere on the board
GPIO32: J14.P$1, J14.P$2, J14.P$3, L1.P$2 (GPIO32); also elsewhere on the board
GPIO40: J163.P$1, J163.P$2, J163.P$3, L1.P$50 (GPIO40/SDAB); also elsewhere on the board
GPIO41: J164.P$1, J164.P$2, J164.P$3, L1.P$49 (GPIO41/SCLB); also elsewhere on the board
GPIO52: J165.P$1, J165.P$2, J165.P$3, J211.P$1, J211.P$2, L1.P$48 (GPIO52)
GPIO56: J169.P$1, J169.P$2, J169.P$3, L1.P$44 (GPIO56/SCITXDC)
GPIO58: J33.P$1, J33.P$2, J33.P$3, L1.P$15 (GPIO58/SPISIMOA)
GPIO59: J32.P$1, J32.P$2, J32.P$3, L1.P$14 (GPIO59/SPISOMIA)
GPIO60: J19.P$1, J19.P$2, J19.P$3, J249.P$1, J249.P$2, L1.P$7 (GPIO60/SPICLKA)
GPIO61: J101.P$1, J101.P$2, J101.P$3, J250.P$1, J250.P$2, L1.P$19 (GPIO61)
GPIO63: J158.P$1, J158.P$2, J158.P$3, J204.P$1, J204.P$2, L1.P$55 (GPIO63/SPISIMOB)
GPIO64: J159.P$1, J159.P$2, J159.P$3, J205.P$1, J205.P$2, L1.P$54 (GPIO64/SPISOMIB)
GPIO65: J166.P$1, J166.P$2, J166.P$3, J206.P$1, J206.P$2, L1.P$47 (GPIO65/SPICLKB)
GPIO66: J154.P$1, J154.P$2, J154.P$3, J207.P$1, J207.P$2, L1.P$59 (GPIO66)
GPIO67: J17.P$1, J17.P$2, J17.P$3, J232.P$1, J232.P$2, L1.P$5 (GPIO67)
GPIO94: J167.P$1, J167.P$2, J167.P$3, J233.P$1, J233.P$2, L1.P$46 (GPIO94)
GPIO95: J176.P$1, J176.P$2, J176.P$3, J241.P$1, J241.P$2, L1.P$42 (GPIO95)
GPIO97: J168.P$1, J168.P$2, J168.P$3, J234.P$1, J234.P$2, L1.P$45 (GPIO97)
GPIO104: J28.P$1, J28.P$2, J28.P$3, L1.P$10 (GPIO104/SDAA)
GPIO105: J21.P$1, J21.P$2, J21.P$3, L1.P$9 (GPIO105/SCLA)
GPIO111: J18.P$1, J18.P$2, J18.P$3, J235.P$1, J235.P$2, L1.P$6 (GPIO111)
GPIO122: J99.P$1, J99.P$2, J99.P$3, L1.P$17 (GPIO122); also elsewhere on the board
GPIO123: J100.P$1, J100.P$2, J100.P$3, L1.P$18 (GPIO123); also elsewhere on the board
GPIO124: J31.P$1, J31.P$2, J31.P$3, L1.P$13 (GPIO124); also elsewhere on the board
GPIO125: J30.P$1, J30.P$2, J30.P$3, L1.P$12 (GPIO125); also elsewhere on the board
GPIO130: J156.P$1, J156.P$2, J156.P$3, J236.P$1, J236.P$2, L1.P$57 (GPIO130)
GPIO131: J155.P$1, J155.P$2, J155.P$3, J237.P$1, J237.P$2, L1.P$58 (GPIO131)
GPIO139: J170.P$1, J170.P$2, J170.P$3, L1.P$43 (GPIO139/SCIRXDC)
unnamed: R24.1, R25.2, U7.P$5 (ADJ)
unnamed: LED_5V1.A, R26.1
unnamed: LED_3.3V1.A, R27.1
unnamed: J125.P$1, J125.P$2, J125.P$3, U$1.3 (P3_SCLK)
unnamed: J126.P$1, J126.P$2, J126.P$3, U$1.4 (P4_SDA/SPIMOSI)
unnamed: J127.P$1, J127.P$2, J127.P$3, U$1.5 (P5_EDA/AUX-DA)
unnamed: J128.P$1, J128.P$2, J128.P$3, U$1.6 (P6_ECL/AUX-CL)
unnamed: J129.P$1, J129.P$2, J129.P$3, U$1.7 (P7_ADO/SPIMISO)
unnamed: J130.P$1, J130.P$2, J130.P$3, U$1.8 (P8_INT)
unnamed: J131.P$1, J131.P$2, J131.P$3, U$1.9 (P9_NCS)
unnamed: J132.P$1, J132.P$2, J132.P$3, U$1.10 (P10_FSYNC)
POWER: C3.1, C5.1, DCDC3.3V.1, DCDC5V.1, J5.1, POWER.2, S141.P$1, S141.P$2, S141.P$3, S141.P$4, S141.P$5, U6.P$1 (!SHDN), U6.P$2 (IN), U7.P$1 (!SHDN), U7.P$2 (IN); also elsewhere on the board
RESET: J98.P$1, J98.P$2, J98.P$3, L1.P$16 (RST)
RESET_2: J157.P$1, J157.P$2, J157.P$3, L1.P$56 (RST_2)
VCC: J10.P$1, J10.P$2, J10.P$3, J123.P$1, J123.P$2, J123.P$3, J177.P$1, J177.P$2, J177.P$3, JP1.2, L1.P$1 (3.3V_1), L1.P$41 (3.3V_2), R27.2, U$1.1 (P1_VCC); also elsewhere on the board
V_REG: C4.1, DCDC3.3V.3, JP1.1, U6.P$4 (OUT), U6.P$5 (SENSE)

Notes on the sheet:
This is for the Buzzer

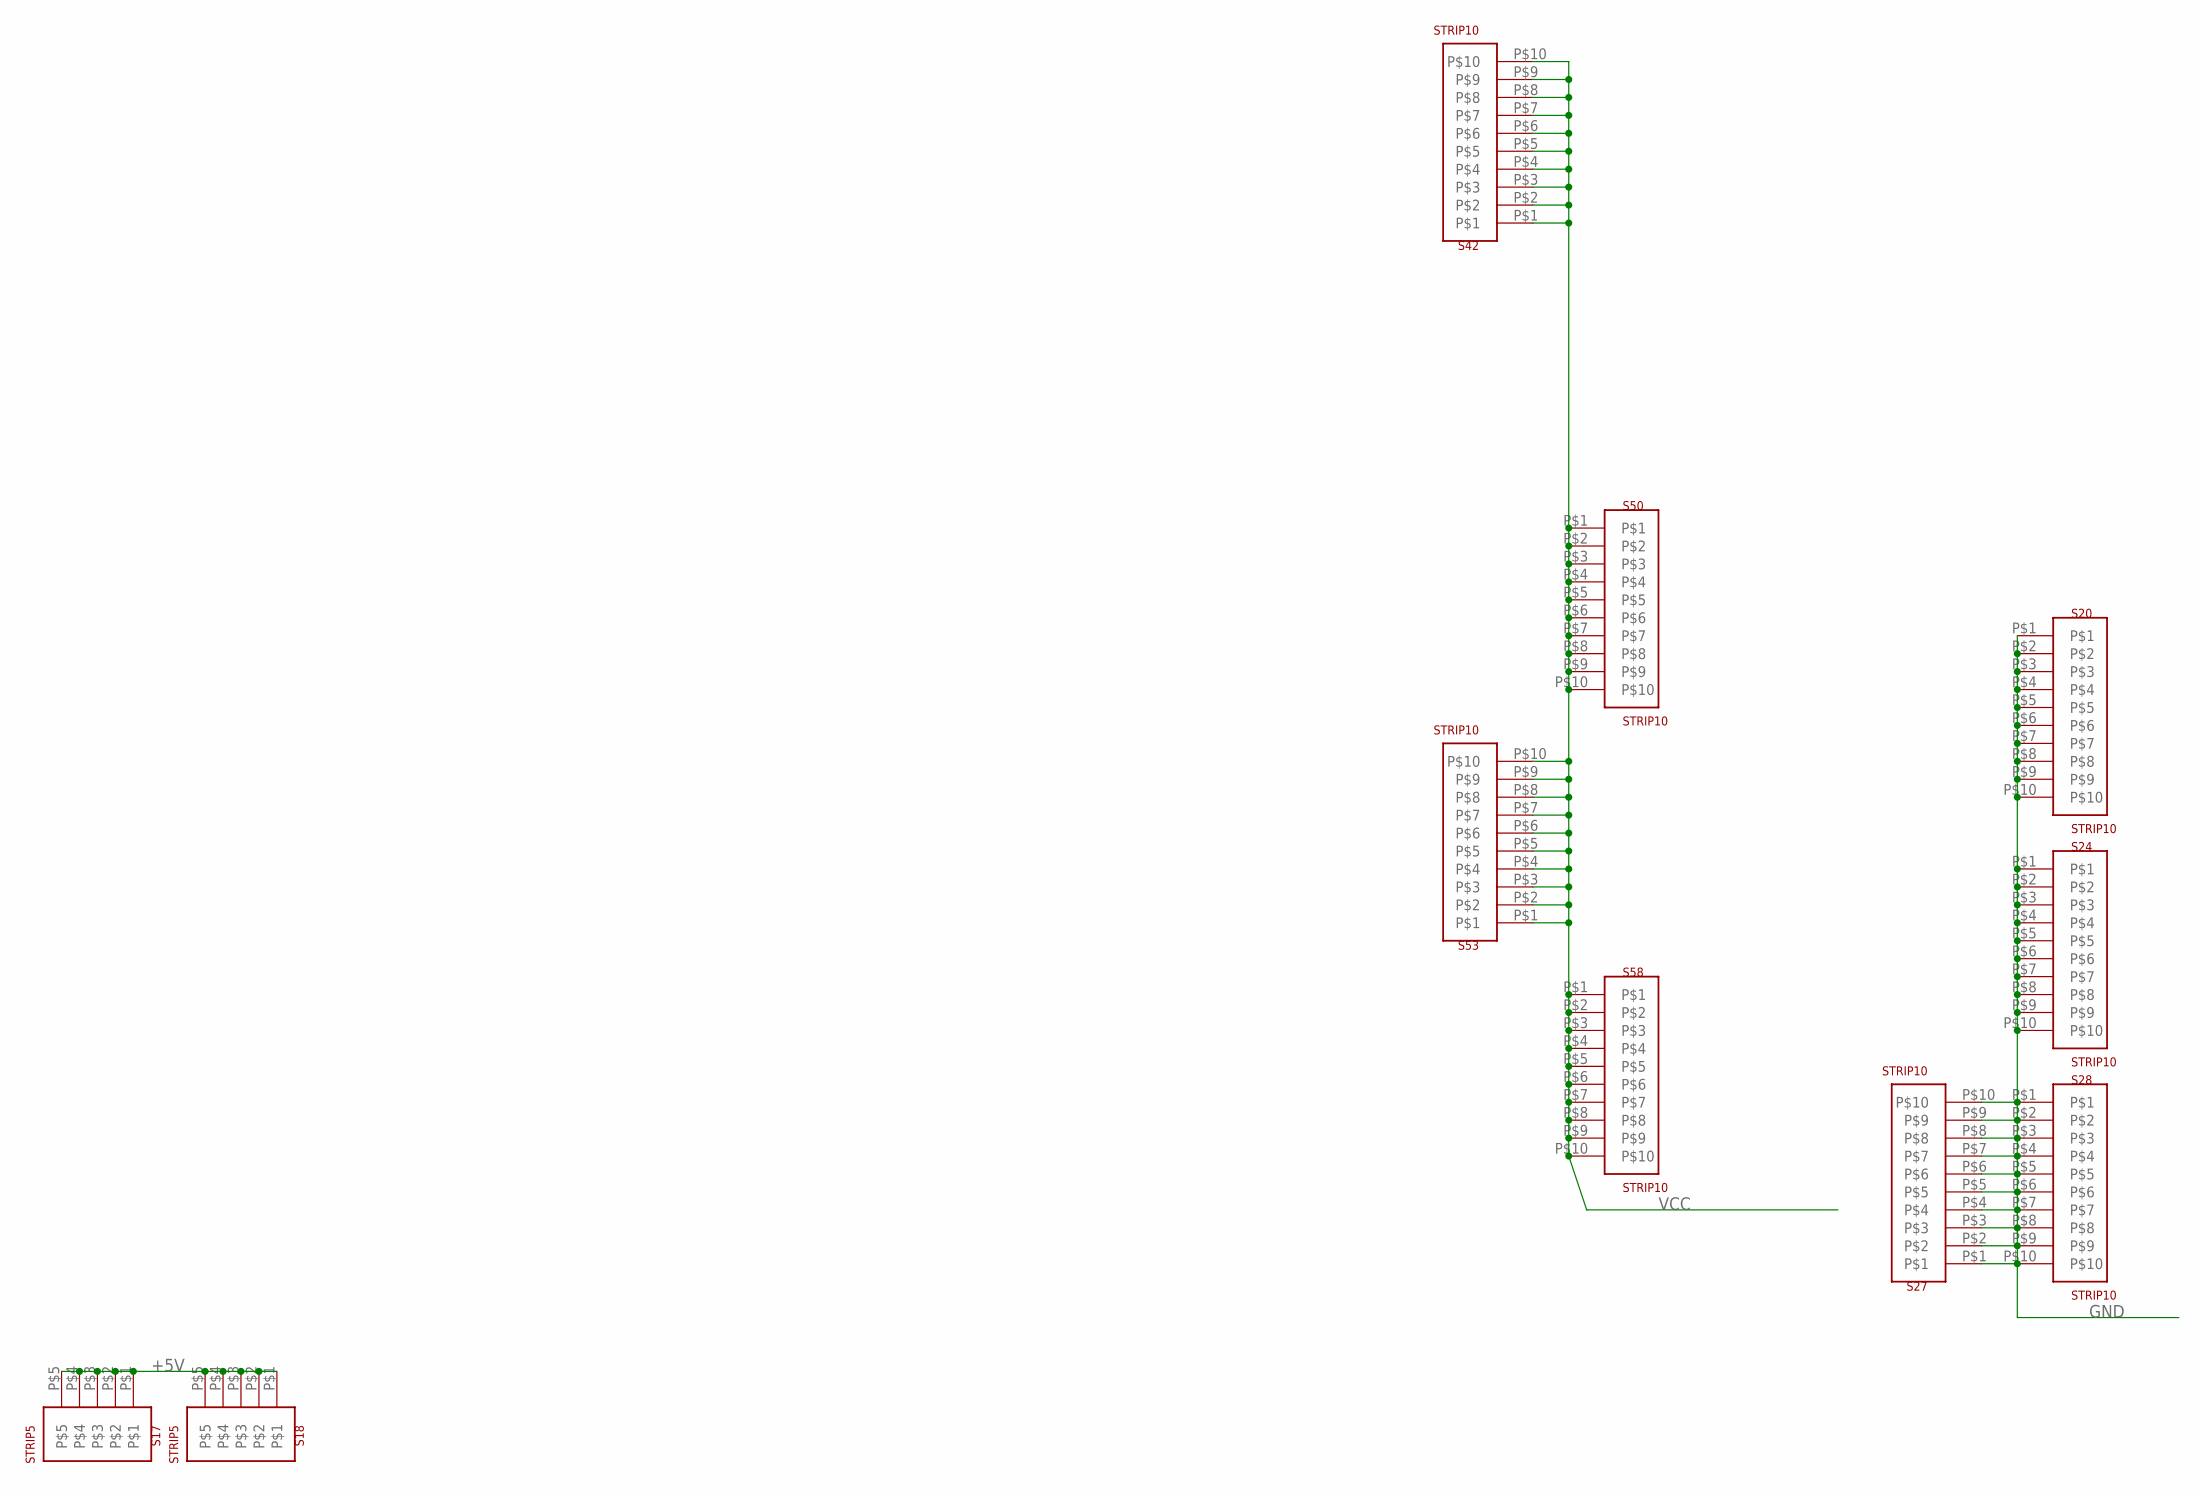
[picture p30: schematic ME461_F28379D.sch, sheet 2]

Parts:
S17, S18: STRIP5
S20, S24, S27, S28, S42, S50, S53, S58: STRIP10

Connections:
+5V: S17.P$1, S17.P$2, S17.P$3, S17.P$4, S17.P$5, S18.P$1, S18.P$2, S18.P$3, S18.P$4, S18.P$5; also elsewhere on the board
GND: S20.P$1, S20.P$2, S20.P$3, S20.P$4, S20.P$5, S20.P$6, S20.P$7, S20.P$8, S20.P$9, S20.P$10, S24.P$1, S24.P$2, S24.P$3, S24.P$4, S24.P$5, S24.P$6, S24.P$7, S24.P$8, S24.P$9, S24.P$10, S27.P$1, S27.P$2, S27.P$3, S27.P$4, S27.P$5, S27.P$6, S27.P$7, S27.P$8, S27.P$9, S27.P$10, S28.P$1, S28.P$2, S28.P$3, S28.P$4, S28.P$5, S28.P$6, S28.P$7, S28.P$8, S28.P$9, S28.P$10; also elsewhere on the board
VCC: S42.P$1, S42.P$2, S42.P$3, S42.P$4, S42.P$5, S42.P$6, S42.P$7, S42.P$8, S42.P$9, S42.P$10, S50.P$1, S50.P$2, S50.P$3, S50.P$4, S50.P$5, S50.P$6, S50.P$7, S50.P$8, S50.P$9, S50.P$10, S53.P$1, S53.P$2, S53.P$3, S53.P$4, S53.P$5, S53.P$6, S53.P$7, S53.P$8, S53.P$9, S53.P$10, S58.P$1, S58.P$2, S58.P$3, S58.P$4, S58.P$5, S58.P$6, S58.P$7, S58.P$8, S58.P$9, S58.P$10; also elsewhere on the board

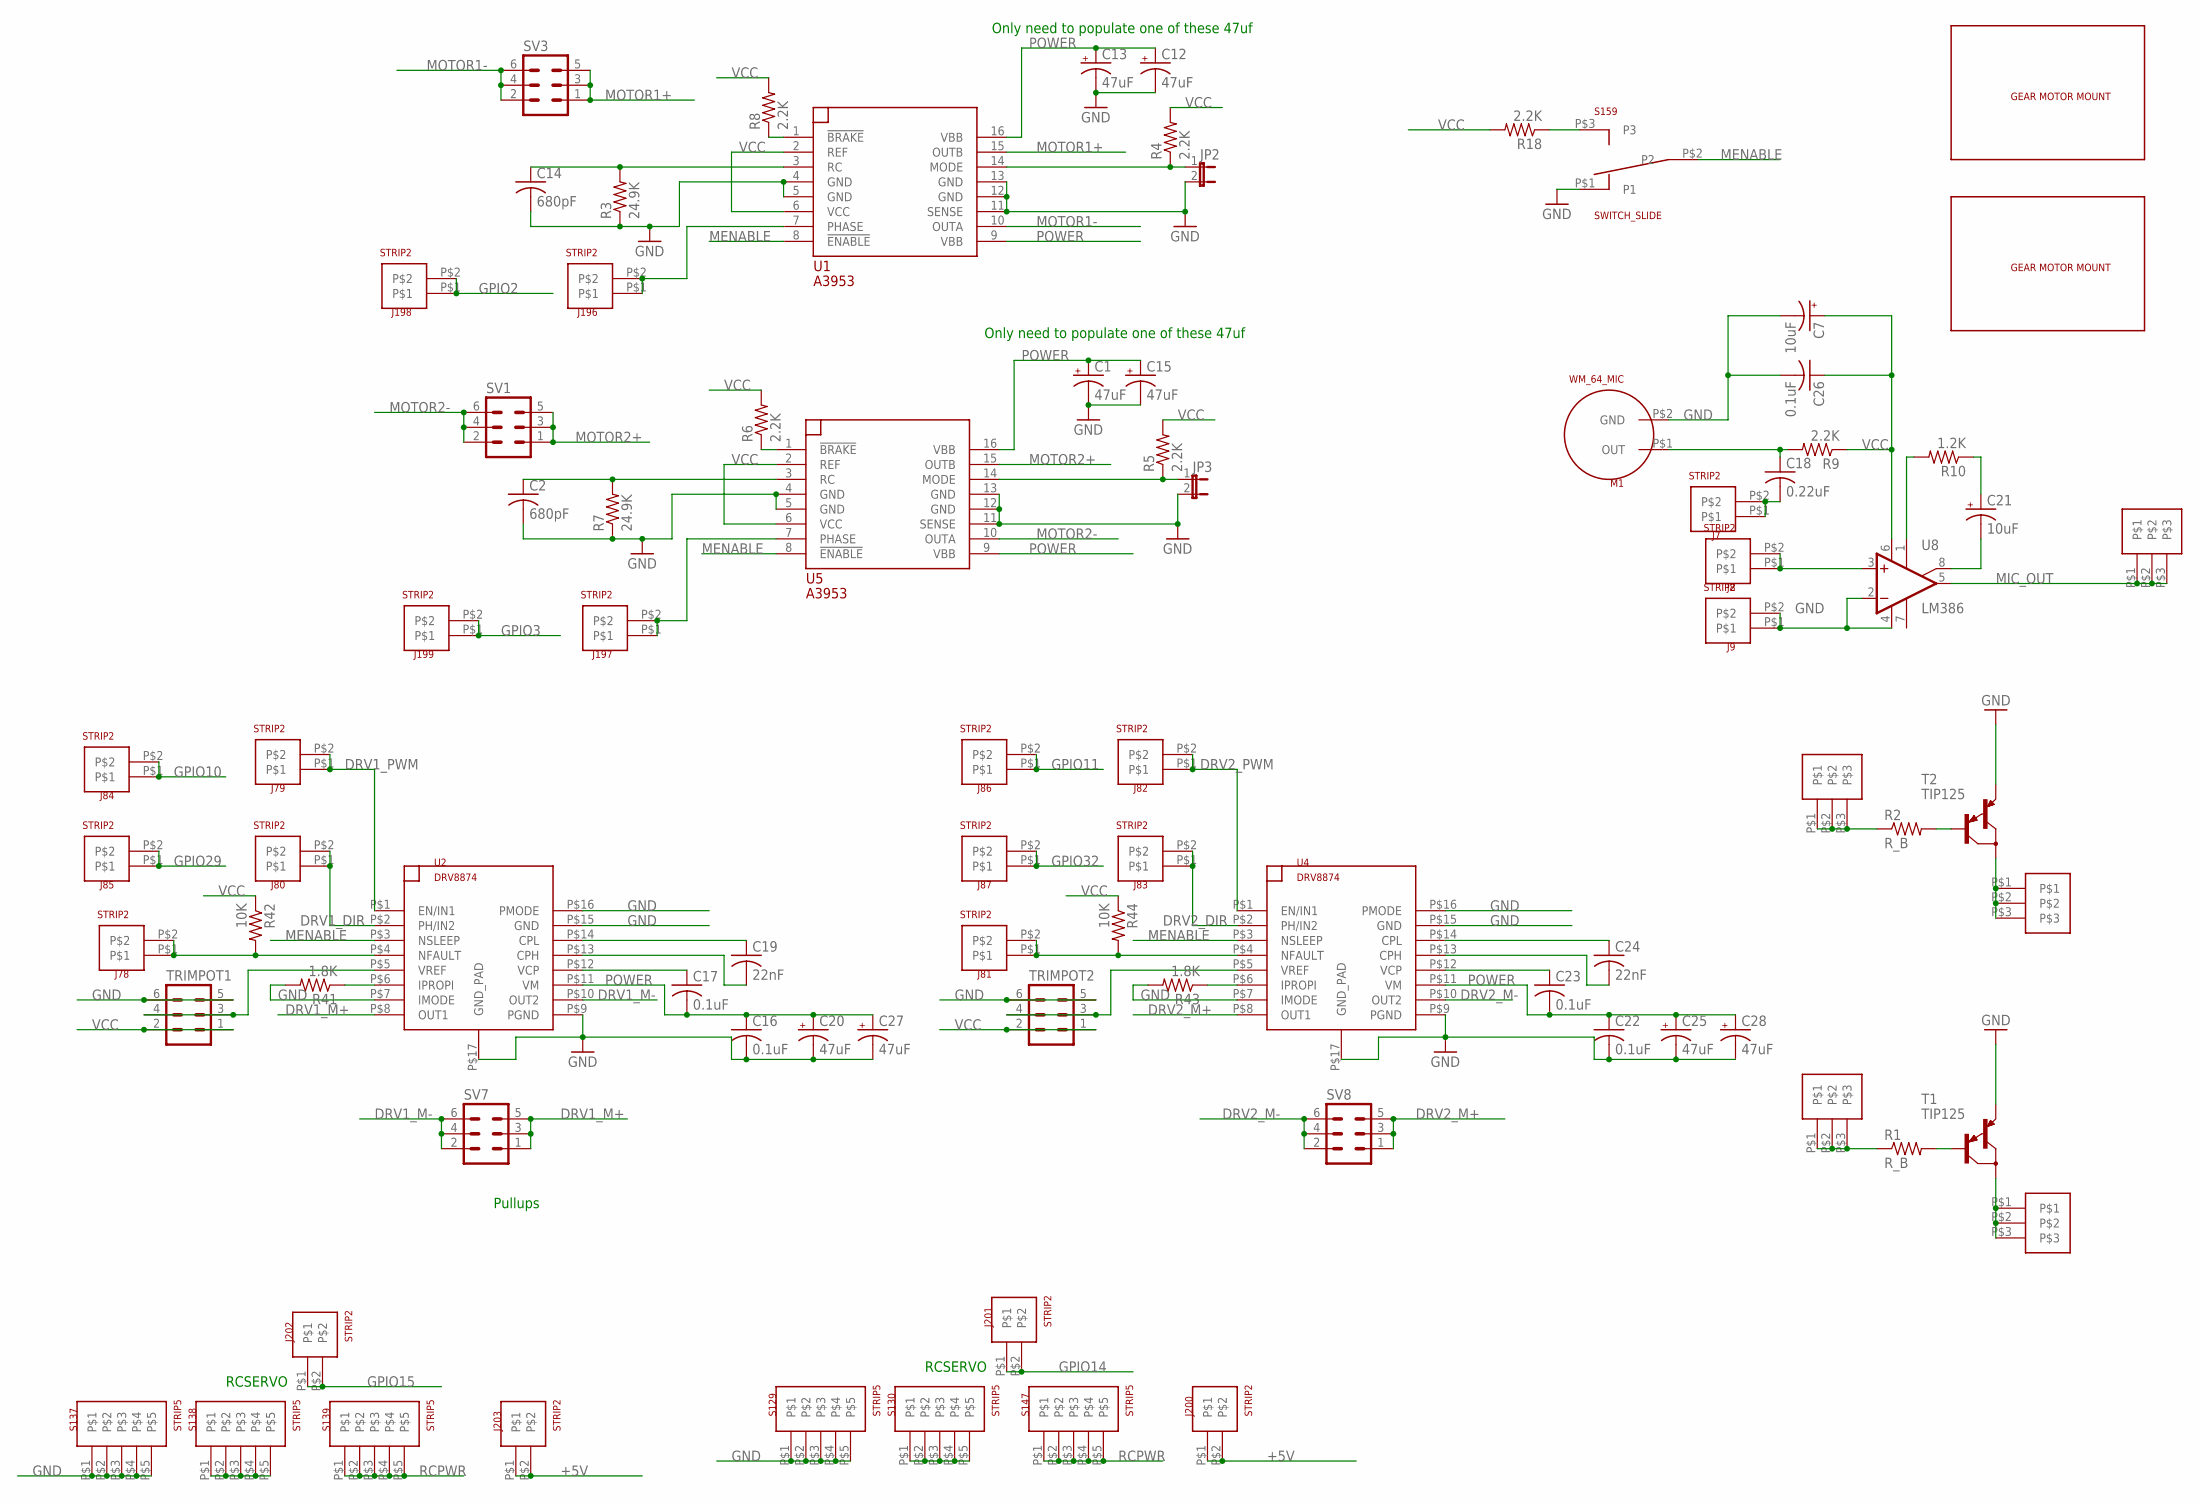
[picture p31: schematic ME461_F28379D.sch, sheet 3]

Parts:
C1, C12, C13, C15, C20, C25, C27, C28: 47uF; 153CLV-0810
C2, C14: 680pF; C1206
C7, C21: 10uF; E2,5-6
C16, C17, C22, C23: 0.1uF; C1206
C18: 0.22uF; C050-025X075
C19, C24: 22nF; C1206
C26: 0.1uF; C050-025X075
J4, J6, J23, J24, J49: STRIP3
J7, J8, J9, J78, J79, J80, J81, J82, J83, J84, J85, J86, J87, J196, J197, J198, J199, J200, J201, J202, J203: STRIP2
JP2, JP3: JP1E; JP1
M1: WM_64_MIC
R1, R2: R_B; 0207/10
R3, R7: 24.9K; M1206
R4, R5, R6, R8, R18: 2.2K; M1206
R9: 2.2K; 0207/10
R10: 1.2K; 0207/10
R41, R43: 1.8K; M1206
R42, R44: 10K; M1206
S129, S130, S137, S138, S139, S147: STRIP5
S159: SWITCH_SLIDE
SV1, SV3, SV7, SV8: MA03-2
T1, T2: TIP125; TO220
TRIMPOT1, TRIMPOT2: MA03-2
U1, U5: A3953; SO16W
U2, U4: DRV8874; HTSSOP16
U8: LM386; DIL08
U$2, U$3: GEARMOTOR_MOUNT

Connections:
+5V: J200.P$1, J200.P$2, J203.P$1, J203.P$2; also elsewhere on the board
DRV1_DIR: J80.P$1, J80.P$2, U2.P$2 (PH/IN2)
DRV1_M+: SV7.1, SV7.3, SV7.5, U2.P$8 (OUT1)
DRV1_M-: SV7.2, SV7.4, SV7.6, U2.P$10 (OUT2)
DRV1_PWM: J79.P$1, J79.P$2, U2.P$1 (EN/IN1)
DRV2_DIR: J83.P$1, J83.P$2, U4.P$2 (PH/IN2)
DRV2_M+: SV8.1, SV8.3, SV8.5, U4.P$8 (OUT1)
DRV2_M-: SV8.2, SV8.4, SV8.6, U4.P$10 (OUT2)
DRV2_PWM: J82.P$1, J82.P$2, U4.P$1 (EN/IN1)
GND: C1.-, C2.2, C7.-, C12.-, C13.-, C14.2, C15.-, C16.2, C20.-, C22.2, C25.-, C26.2, C27.-, C28.-, J9.P$1, J9.P$2, JP2.2, JP3.2, M1.P$2 (GND), R3.1, R7.1, R41.2, R43.2, S129.P$1, S129.P$2, S129.P$3, S129.P$4, S129.P$5, S137.P$1, S137.P$2, S137.P$3, S137.P$4, S137.P$5, S159.P$1 (P1), T1.3 (E), T2.3 (E), TRIMPOT1.5, TRIMPOT1.6, TRIMPOT2.5, TRIMPOT2.6, U1.4 (GND), U1.5 (GND), U1.11 (SENSE), U1.12 (GND), U1.13 (GND), U2.P$7 (IMODE), U2.P$9 (PGND), U2.P$15 (GND), U2.P$16 (PMODE), U2.P$17 (GND_PAD), U4.P$7 (IMODE), U4.P$9 (PGND), U4.P$15 (GND), U4.P$16 (PMODE), U4.P$17 (GND_PAD), U5.4 (GND), U5.5 (GND), U5.11 (SENSE), U5.12 (GND), U5.13 (GND), U8.2 (-IN), U8.4 (GND); also elsewhere on the board
GPIO2: J198.P$1, J198.P$2; also elsewhere on the board
GPIO3: J199.P$1, J199.P$2; also elsewhere on the board
GPIO10: J84.P$1, J84.P$2; also elsewhere on the board
GPIO11: J86.P$1, J86.P$2; also elsewhere on the board
GPIO14: J201.P$1, J201.P$2; also elsewhere on the board
GPIO15: J202.P$1, J202.P$2; also elsewhere on the board
GPIO29: J85.P$1, J85.P$2; also elsewhere on the board
GPIO32: J87.P$1, J87.P$2; also elsewhere on the board
MENABLE: S159.P$2 (P2), U1.8 (!ENABLE), U2.P$3 (NSLEEP), U4.P$3 (NSLEEP), U5.8 (!ENABLE)
MIC_OUT: J49.P$1, J49.P$2, J49.P$3, U8.5 (OUT)
MOTOR1+: SV3.1, SV3.3, SV3.5, U1.15 (OUTB)
MOTOR1-: SV3.2, SV3.4, SV3.6, U1.10 (OUTA)
MOTOR2+: SV1.1, SV1.3, SV1.5, U5.15 (OUTB)
MOTOR2-: SV1.2, SV1.4, SV1.6, U5.10 (OUTA)
unnamed: R2.2, T2.1 (B)
unnamed: R1.2, T1.1 (B)
unnamed: S138.P$1, S138.P$2, S138.P$3, S138.P$4, S138.P$5
unnamed: C21.-, U8.8 (GAIN2)
unnamed: R10.2, U8.1 (GAIN1)
unnamed: C21.+, R10.1
unnamed: C18.2, J7.P$1, J7.P$2
unnamed: C18.1, M1.P$1 (OUT), R9.2
unnamed: R6.1, U5.1 (!BRAKE)
unnamed: C2.1, R7.2, U5.3 (RC)
unnamed: R8.1, U1.1 (!BRAKE)
unnamed: C14.1, R3.2, U1.3 (RC)
unnamed: JP2.1, R4.1, U1.14 (MODE)
unnamed: R18.1, S159.P$3 (P3)
unnamed: JP3.1, R5.1, U5.14 (MODE)
unnamed: C19.1, U2.P$14 (CPL)
unnamed: C19.2, U2.P$13 (CPH)
unnamed: C17.1, U2.P$12 (VCP)
unnamed: R43.1, U4.P$6 (IPROPI)
unnamed: R41.1, U2.P$6 (IPROPI)
unnamed: J78.P$1, J78.P$2, R42.2, U2.P$4 (NFAULT)
unnamed: TRIMPOT1.3, TRIMPOT1.4, U2.P$5 (VREF)
unnamed: C24.1, U4.P$14 (CPL)
unnamed: C24.2, U4.P$13 (CPH)
unnamed: C23.1, U4.P$12 (VCP)
unnamed: J81.P$1, J81.P$2, R44.2, U4.P$4 (NFAULT)
unnamed: TRIMPOT2.3, TRIMPOT2.4, U4.P$5 (VREF)
unnamed: S130.P$1, S130.P$2, S130.P$3, S130.P$4, S130.P$5
unnamed: J8.P$1, J8.P$2, U8.3 (+IN)
unnamed: J196.P$1, J196.P$2, U1.7 (PHASE)
unnamed: J197.P$1, J197.P$2, U5.7 (PHASE)
POWER: C1.+, C12.+, C13.+, C15.+, C16.1, C17.2, C20.+, C22.1, C23.2, C25.+, C27.+, C28.+, U1.9 (VBB), U1.16 (VBB), U2.P$11 (VM), U4.P$11 (VM), U5.9 (VBB), U5.16 (VBB); also elsewhere on the board
RCPWR: S139.P$1, S139.P$2, S139.P$3, S139.P$4, S139.P$5, S147.P$1, S147.P$2, S147.P$3, S147.P$4, S147.P$5
TR_BASE: J6.P$1, J6.P$2, J6.P$3, R1.1
TR_BASE1: J24.P$1, J24.P$2, J24.P$3, R2.1
TR_LOAD: J4.P$1, J4.P$2, J4.P$3, T1.2 (C)
TR_LOAD1: J23.P$1, J23.P$2, J23.P$3, T2.2 (C)
VCC: C7.+, C26.1, R4.2, R5.2, R6.2, R8.2, R9.1, R18.2, R42.1, R44.1, TRIMPOT1.1, TRIMPOT1.2, TRIMPOT2.1, TRIMPOT2.2, U1.2 (REF), U1.6 (VCC), U5.2 (REF), U5.6 (VCC), U8.6 (VS); also elsewhere on the board

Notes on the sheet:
Pullups
RCSERVO
Only need to populate one of these 47uf

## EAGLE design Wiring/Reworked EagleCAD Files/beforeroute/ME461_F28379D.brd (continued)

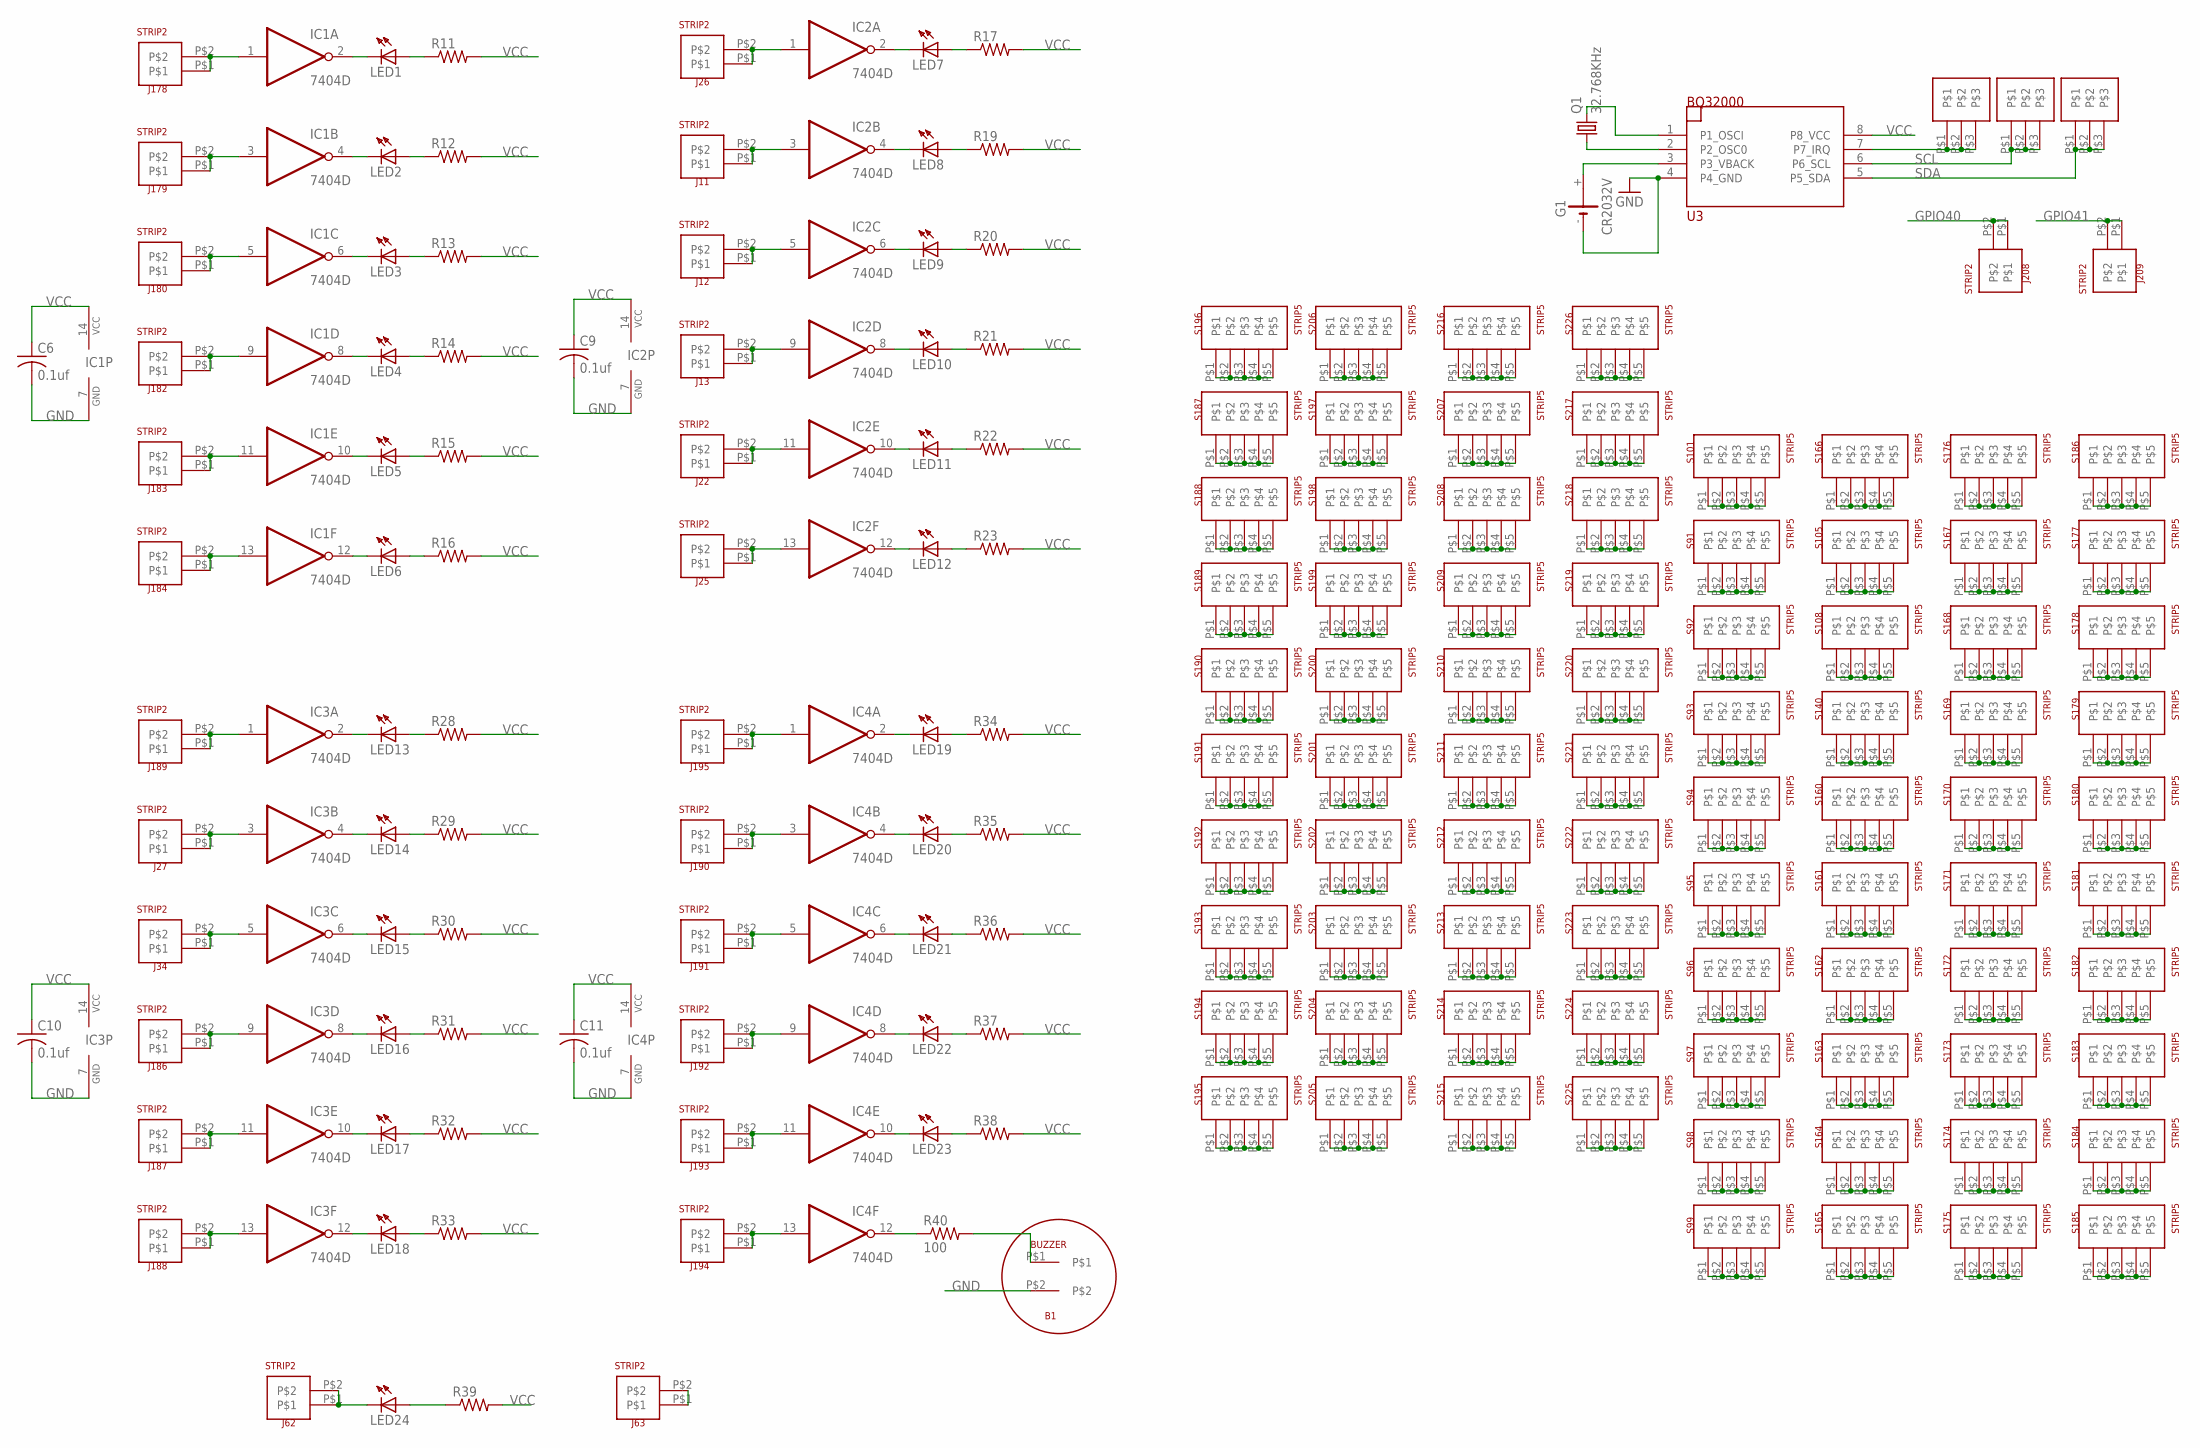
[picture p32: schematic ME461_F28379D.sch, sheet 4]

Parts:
B1: BUZZER
C6, C9, C10, C11: 0.1uf; C1206
G1: CR2032V
IC1, IC2, IC3, IC4: 7404D; SO14
J1, J2, J3: STRIP3
J11, J12, J13, J22, J25, J26, J27, J34, J62, J63, J178, J179, J180, J182, J183, J184, J186, J187, J188, J189, J190, J191, J192, J193, J194, J195, J208, J209: STRIP2
LED1, LED2, LED3, LED4, LED5, LED6, LED7, LED8, LED9, LED10, LED11, LED12, LED13, LED14, LED15, LED16, LED17, LED18, LED19, LED20, LED21, LED22, LED23, LED24: LED3MM
Q1: 32.768KHz; TC26H
R11, R12, R13, R14, R15, R16, R17, R19, R20, R21, R22, R23, R28, R29, R30, R31, R32, R33, R34, R35, R36, R37, R38, R39: R-US_R1206; R1206
R40: 100; R1206
S91, S92, S93, S94, S95, S96, S97, S98, S99, S101, S105, S108, S140, S160, S161, S162, S163, S164, S165, S166, S167, S168, S169, S170, S171, S172, S173, S174, S175, S176, S177, S178, S179, S180, S181, S182, S183, S184, S185, S186, S187, S188, S189, S190, S191, S192, S193, S194, S195, S196, S197, S198, S199, S200, S201, S202, S203, S204, S205, S206, S207, S208, S209, S210, S211, S212, S213, S214, S215, S216, S217, S218, S219, S220, S221, S222, S223, S224, S225, S226: STRIP5
U3: BQ32000; SO08

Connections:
GND: B1.P$2, C6.2, C9.2, C10.2, C11.2, G1.-, IC1.7 (GND), IC2.7 (GND), IC3.7 (GND), IC4.7 (GND), U3.4 (P4_GND); also elsewhere on the board
GPIO40: J208.P$1, J208.P$2; also elsewhere on the board
GPIO41: J209.P$1, J209.P$2; also elsewhere on the board
unnamed: J62.P$1, J62.P$2, LED24.K (C)
unnamed: IC4.12 (O), R40.1
unnamed: B1.P$1, R40.2
unnamed: Q1.1, U3.2 (P2_OSC0)
unnamed: J63.P$1, J63.P$2
unnamed: Q1.2, U3.1 (P1_OSCI)
unnamed: J1.P$1, J1.P$2, J1.P$3, U3.7 (P7_IRQ)
unnamed: G1.+, U3.3 (P3_VBACK)
unnamed: IC2.1 (I), J26.P$1, J26.P$2
unnamed: IC2.2 (O), LED7.K (C)
unnamed: LED7.A, R17.1
unnamed: IC2.3 (I), J11.P$1, J11.P$2
unnamed: IC2.4 (O), LED8.K (C)
unnamed: LED8.A, R19.1
unnamed: IC2.5 (I), J12.P$1, J12.P$2
unnamed: IC2.6 (O), LED9.K (C)
unnamed: S91.P$1, S91.P$2, S91.P$3, S91.P$4, S91.P$5
unnamed: S92.P$1, S92.P$2, S92.P$3, S92.P$4, S92.P$5
unnamed: S93.P$1, S93.P$2, S93.P$3, S93.P$4, S93.P$5
unnamed: S94.P$1, S94.P$2, S94.P$3, S94.P$4, S94.P$5
unnamed: S95.P$1, S95.P$2, S95.P$3, S95.P$4, S95.P$5
unnamed: S96.P$1, S96.P$2, S96.P$3, S96.P$4, S96.P$5
unnamed: S97.P$1, S97.P$2, S97.P$3, S97.P$4, S97.P$5
unnamed: S98.P$1, S98.P$2, S98.P$3, S98.P$4, S98.P$5
unnamed: S99.P$1, S99.P$2, S99.P$3, S99.P$4, S99.P$5
unnamed: S101.P$1, S101.P$2, S101.P$3, S101.P$4, S101.P$5
unnamed: S105.P$1, S105.P$2, S105.P$3, S105.P$4, S105.P$5
unnamed: S108.P$1, S108.P$2, S108.P$3, S108.P$4, S108.P$5
unnamed: S140.P$1, S140.P$2, S140.P$3, S140.P$4, S140.P$5
unnamed: S160.P$1, S160.P$2, S160.P$3, S160.P$4, S160.P$5
unnamed: S161.P$1, S161.P$2, S161.P$3, S161.P$4, S161.P$5
unnamed: S162.P$1, S162.P$2, S162.P$3, S162.P$4, S162.P$5
unnamed: S163.P$1, S163.P$2, S163.P$3, S163.P$4, S163.P$5
unnamed: S164.P$1, S164.P$2, S164.P$3, S164.P$4, S164.P$5
unnamed: S165.P$1, S165.P$2, S165.P$3, S165.P$4, S165.P$5
unnamed: S166.P$1, S166.P$2, S166.P$3, S166.P$4, S166.P$5
unnamed: S167.P$1, S167.P$2, S167.P$3, S167.P$4, S167.P$5
unnamed: S168.P$1, S168.P$2, S168.P$3, S168.P$4, S168.P$5
unnamed: S169.P$1, S169.P$2, S169.P$3, S169.P$4, S169.P$5
unnamed: S170.P$1, S170.P$2, S170.P$3, S170.P$4, S170.P$5
unnamed: S171.P$1, S171.P$2, S171.P$3, S171.P$4, S171.P$5
unnamed: S172.P$1, S172.P$2, S172.P$3, S172.P$4, S172.P$5
unnamed: S173.P$1, S173.P$2, S173.P$3, S173.P$4, S173.P$5
unnamed: S174.P$1, S174.P$2, S174.P$3, S174.P$4, S174.P$5
unnamed: S175.P$1, S175.P$2, S175.P$3, S175.P$4, S175.P$5
unnamed: S176.P$1, S176.P$2, S176.P$3, S176.P$4, S176.P$5
unnamed: S177.P$1, S177.P$2, S177.P$3, S177.P$4, S177.P$5
unnamed: S178.P$1, S178.P$2, S178.P$3, S178.P$4, S178.P$5
unnamed: S179.P$1, S179.P$2, S179.P$3, S179.P$4, S179.P$5
unnamed: S180.P$1, S180.P$2, S180.P$3, S180.P$4, S180.P$5
unnamed: S181.P$1, S181.P$2, S181.P$3, S181.P$4, S181.P$5
unnamed: S182.P$1, S182.P$2, S182.P$3, S182.P$4, S182.P$5
unnamed: S183.P$1, S183.P$2, S183.P$3, S183.P$4, S183.P$5
unnamed: S184.P$1, S184.P$2, S184.P$3, S184.P$4, S184.P$5
unnamed: S185.P$1, S185.P$2, S185.P$3, S185.P$4, S185.P$5
unnamed: S186.P$1, S186.P$2, S186.P$3, S186.P$4, S186.P$5
unnamed: S187.P$1, S187.P$2, S187.P$3, S187.P$4, S187.P$5
unnamed: S188.P$1, S188.P$2, S188.P$3, S188.P$4, S188.P$5
unnamed: S189.P$1, S189.P$2, S189.P$3, S189.P$4, S189.P$5
unnamed: S190.P$1, S190.P$2, S190.P$3, S190.P$4, S190.P$5
unnamed: S191.P$1, S191.P$2, S191.P$3, S191.P$4, S191.P$5
unnamed: S192.P$1, S192.P$2, S192.P$3, S192.P$4, S192.P$5
unnamed: S193.P$1, S193.P$2, S193.P$3, S193.P$4, S193.P$5
unnamed: S194.P$1, S194.P$2, S194.P$3, S194.P$4, S194.P$5
unnamed: S195.P$1, S195.P$2, S195.P$3, S195.P$4, S195.P$5
unnamed: S196.P$1, S196.P$2, S196.P$3, S196.P$4, S196.P$5
unnamed: S197.P$1, S197.P$2, S197.P$3, S197.P$4, S197.P$5
unnamed: S198.P$1, S198.P$2, S198.P$3, S198.P$4, S198.P$5
unnamed: S199.P$1, S199.P$2, S199.P$3, S199.P$4, S199.P$5
unnamed: S200.P$1, S200.P$2, S200.P$3, S200.P$4, S200.P$5
unnamed: S201.P$1, S201.P$2, S201.P$3, S201.P$4, S201.P$5
unnamed: S202.P$1, S202.P$2, S202.P$3, S202.P$4, S202.P$5
unnamed: S203.P$1, S203.P$2, S203.P$3, S203.P$4, S203.P$5
unnamed: S204.P$1, S204.P$2, S204.P$3, S204.P$4, S204.P$5
unnamed: S205.P$1, S205.P$2, S205.P$3, S205.P$4, S205.P$5
unnamed: S206.P$1, S206.P$2, S206.P$3, S206.P$4, S206.P$5
unnamed: S207.P$1, S207.P$2, S207.P$3, S207.P$4, S207.P$5
unnamed: S208.P$1, S208.P$2, S208.P$3, S208.P$4, S208.P$5
unnamed: S209.P$1, S209.P$2, S209.P$3, S209.P$4, S209.P$5
unnamed: S210.P$1, S210.P$2, S210.P$3, S210.P$4, S210.P$5
unnamed: S211.P$1, S211.P$2, S211.P$3, S211.P$4, S211.P$5
unnamed: S212.P$1, S212.P$2, S212.P$3, S212.P$4, S212.P$5
unnamed: S213.P$1, S213.P$2, S213.P$3, S213.P$4, S213.P$5
unnamed: S214.P$1, S214.P$2, S214.P$3, S214.P$4, S214.P$5
unnamed: S215.P$1, S215.P$2, S215.P$3, S215.P$4, S215.P$5
unnamed: S216.P$1, S216.P$2, S216.P$3, S216.P$4, S216.P$5
unnamed: S217.P$1, S217.P$2, S217.P$3, S217.P$4, S217.P$5
unnamed: S218.P$1, S218.P$2, S218.P$3, S218.P$4, S218.P$5
unnamed: S219.P$1, S219.P$2, S219.P$3, S219.P$4, S219.P$5
unnamed: S220.P$1, S220.P$2, S220.P$3, S220.P$4, S220.P$5
unnamed: S221.P$1, S221.P$2, S221.P$3, S221.P$4, S221.P$5
unnamed: S222.P$1, S222.P$2, S222.P$3, S222.P$4, S222.P$5
unnamed: S223.P$1, S223.P$2, S223.P$3, S223.P$4, S223.P$5
unnamed: S224.P$1, S224.P$2, S224.P$3, S224.P$4, S224.P$5
unnamed: S225.P$1, S225.P$2, S225.P$3, S225.P$4, S225.P$5
unnamed: S226.P$1, S226.P$2, S226.P$3, S226.P$4, S226.P$5
unnamed: IC1.1 (I), J178.P$1, J178.P$2
unnamed: IC1.2 (O), LED1.K (C)
unnamed: LED1.A, R11.1
unnamed: IC1.3 (I), J179.P$1, J179.P$2
unnamed: IC1.4 (O), LED2.K (C)
unnamed: LED2.A, R12.1
unnamed: IC1.5 (I), J180.P$1, J180.P$2
unnamed: IC1.6 (O), LED3.K (C)
unnamed: LED3.A, R13.1
unnamed: IC1.9 (I), J182.P$1, J182.P$2
unnamed: IC1.8 (O), LED4.K (C)
unnamed: LED4.A, R14.1
unnamed: IC1.11 (I), J183.P$1, J183.P$2
unnamed: IC1.10 (O), LED5.K (C)
unnamed: LED5.A, R15.1
unnamed: IC1.13 (I), J184.P$1, J184.P$2
unnamed: IC1.12 (O), LED6.K (C)
unnamed: LED6.A, R16.1
unnamed: LED9.A, R20.1
unnamed: IC2.9 (I), J13.P$1, J13.P$2
unnamed: IC2.8 (O), LED10.K (C)
unnamed: LED10.A, R21.1
unnamed: IC2.11 (I), J22.P$1, J22.P$2
unnamed: IC2.10 (O), LED11.K (C)
unnamed: LED11.A, R22.1
unnamed: IC2.13 (I), J25.P$1, J25.P$2
unnamed: IC2.12 (O), LED12.K (C)
unnamed: LED12.A, R23.1
unnamed: IC3.1 (I), J189.P$1, J189.P$2
unnamed: IC3.2 (O), LED13.K (C)
unnamed: LED13.A, R28.1
unnamed: IC3.3 (I), J27.P$1, J27.P$2
unnamed: IC3.4 (O), LED14.K (C)
unnamed: LED14.A, R29.1
unnamed: IC3.5 (I), J34.P$1, J34.P$2
unnamed: IC3.6 (O), LED15.K (C)
unnamed: LED15.A, R30.1
unnamed: IC3.9 (I), J186.P$1, J186.P$2
unnamed: IC3.8 (O), LED16.K (C)
unnamed: LED16.A, R31.1
unnamed: IC3.11 (I), J187.P$1, J187.P$2
unnamed: IC3.10 (O), LED17.K (C)
unnamed: LED17.A, R32.1
unnamed: IC3.13 (I), J188.P$1, J188.P$2
unnamed: IC3.12 (O), LED18.K (C)
unnamed: LED18.A, R33.1
unnamed: IC4.1 (I), J195.P$1, J195.P$2
unnamed: IC4.2 (O), LED19.K (C)
unnamed: LED19.A, R34.1
unnamed: IC4.3 (I), J190.P$1, J190.P$2
unnamed: IC4.4 (O), LED20.K (C)
unnamed: LED20.A, R35.1
unnamed: IC4.5 (I), J191.P$1, J191.P$2
unnamed: IC4.6 (O), LED21.K (C)
unnamed: LED21.A, R36.1
unnamed: IC4.9 (I), J192.P$1, J192.P$2
unnamed: IC4.8 (O), LED22.K (C)
unnamed: LED22.A, R37.1
unnamed: IC4.11 (I), J193.P$1, J193.P$2
unnamed: IC4.10 (O), LED23.K (C)
unnamed: LED23.A, R38.1
unnamed: IC4.13 (I), J194.P$1, J194.P$2
unnamed: LED24.A, R39.1
SCL: J2.P$1, J2.P$2, J2.P$3, U3.6 (P6_SCL)
SDA: J3.P$1, J3.P$2, J3.P$3, U3.5 (P5_SDA)
VCC: C6.1, C9.1, C10.1, C11.1, IC1.14 (VCC), IC2.14 (VCC), IC3.14 (VCC), IC4.14 (VCC), R11.2, R12.2, R13.2, R14.2, R15.2, R16.2, R17.2, R19.2, R20.2, R21.2, R22.2, R23.2, R28.2, R29.2, R30.2, R31.2, R32.2, R33.2, R34.2, R35.2, R36.2, R37.2, R38.2, R39.2, U3.8 (P8_VCC); also elsewhere on the board

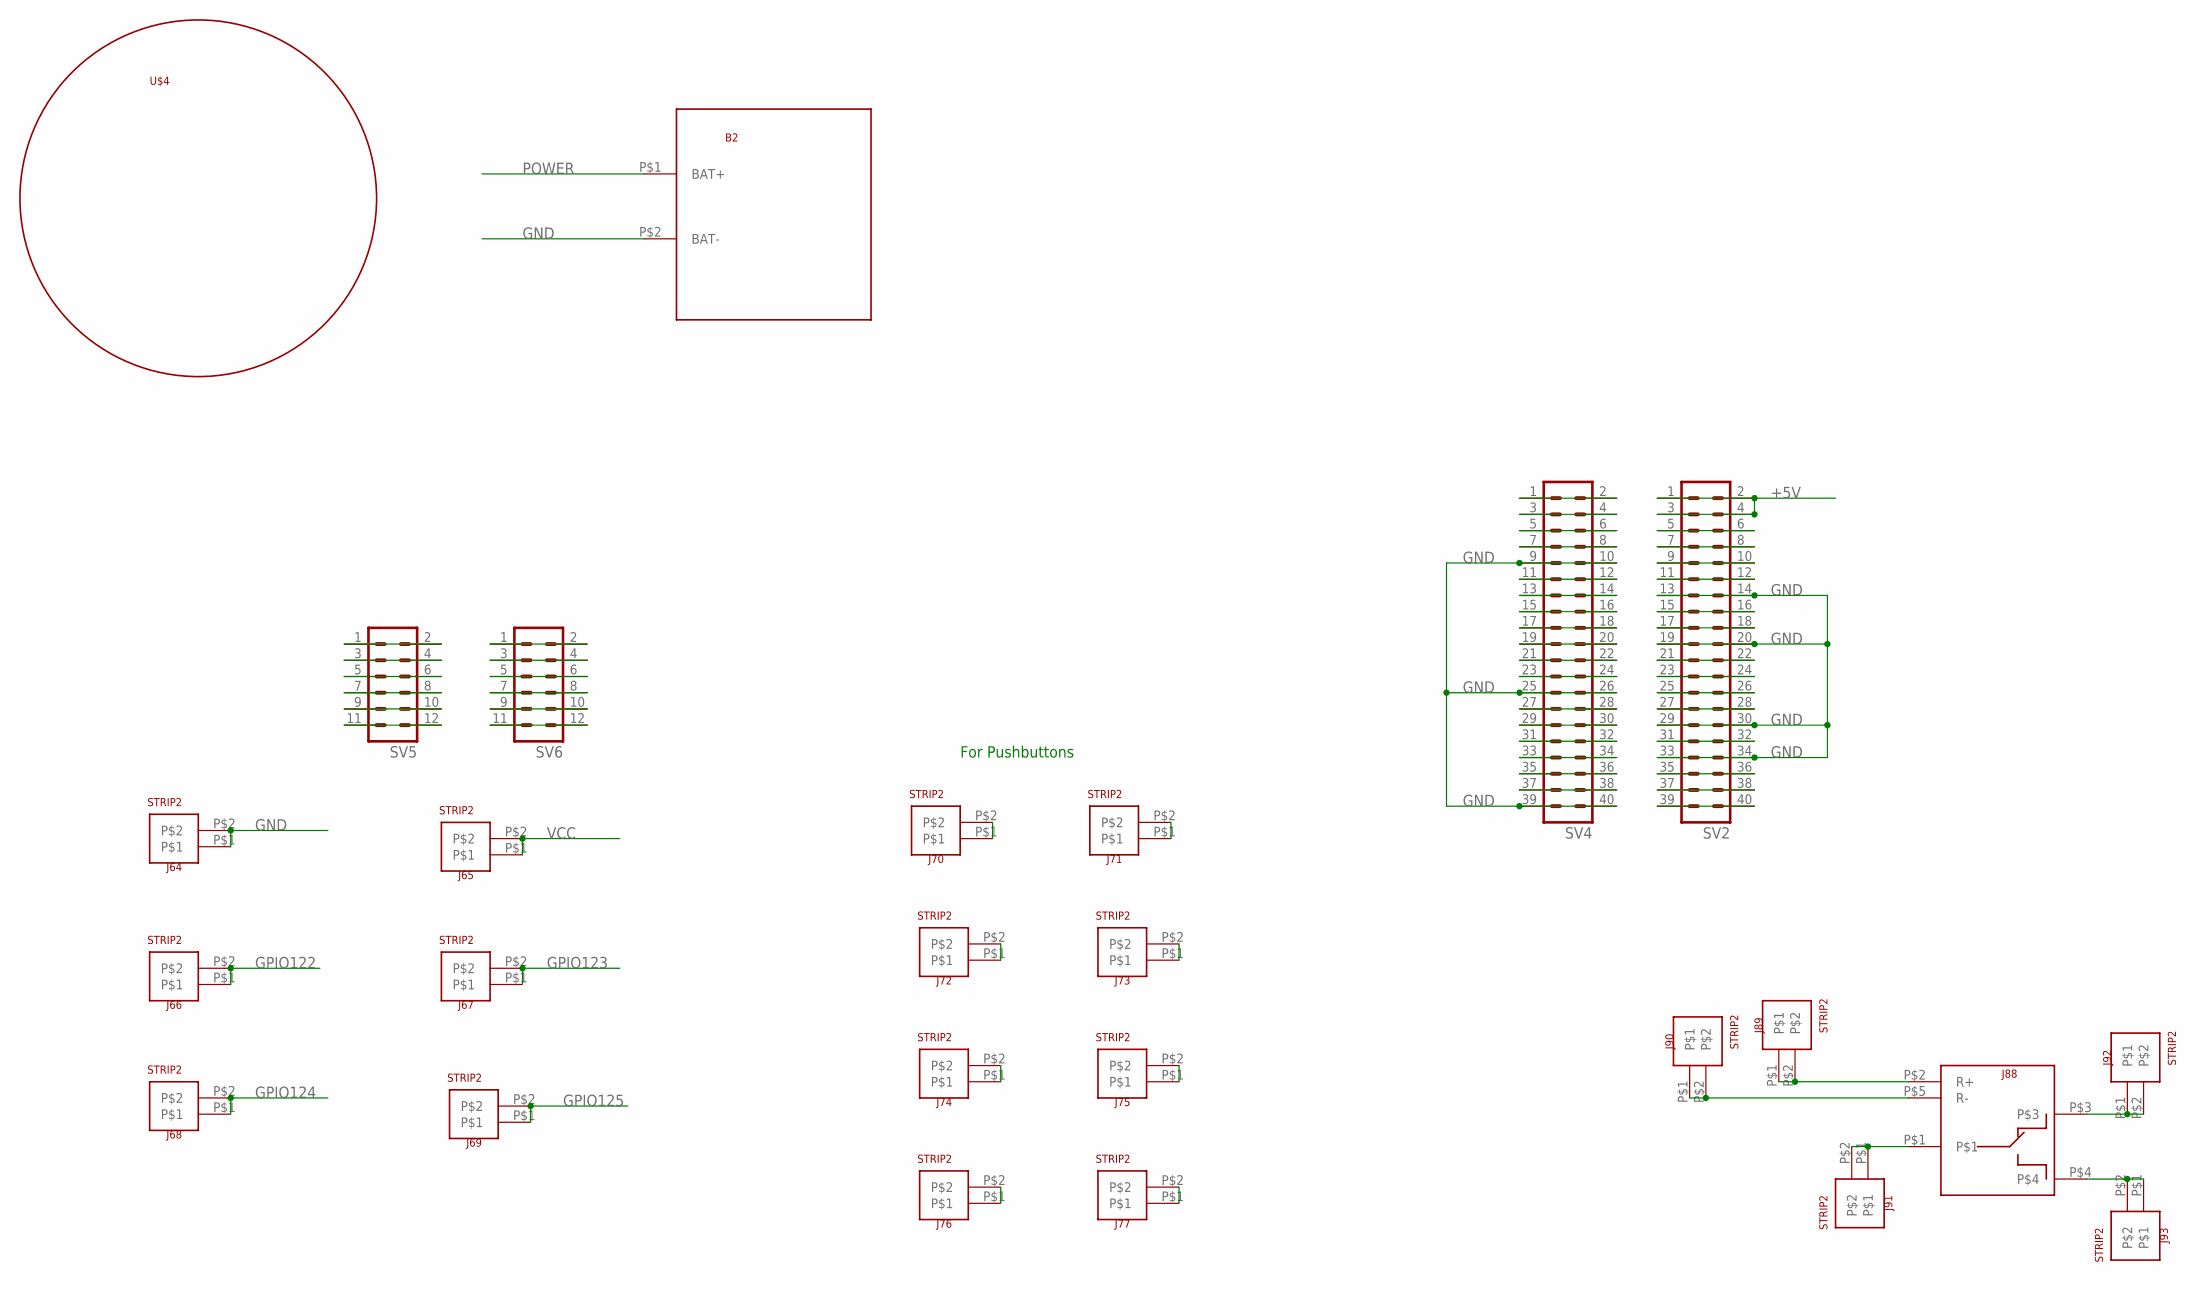
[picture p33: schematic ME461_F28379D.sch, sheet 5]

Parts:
B2: BATTERY_4AA_HOLDER
J64, J65, J66, J67, J68, J69, J70, J71, J72, J73, J74, J75, J76, J77, J89, J90, J91, J92, J93: STRIP2
J88: RELAY_JQC-3F_5V
SV2, SV4: MA20-2
SV5, SV6: MA06-2
U$4: CASTERWHEEL

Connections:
+5V: SV2.1, SV2.2, SV2.3, SV2.4; also elsewhere on the board
GND: B2.P$2 (BAT-), J64.P$1, J64.P$2, SV2.13, SV2.14, SV2.19, SV2.20, SV2.29, SV2.30, SV2.33, SV2.34, SV4.9, SV4.10, SV4.25, SV4.26, SV4.39, SV4.40; also elsewhere on the board
GPIO122: J66.P$1, J66.P$2; also elsewhere on the board
GPIO123: J67.P$1, J67.P$2; also elsewhere on the board
GPIO124: J68.P$1, J68.P$2; also elsewhere on the board
GPIO125: J69.P$1, J69.P$2; also elsewhere on the board
unnamed: SV4.1, SV4.2
unnamed: SV5.1, SV5.2
unnamed: SV5.3, SV5.4
unnamed: SV5.5, SV5.6
unnamed: SV4.3, SV4.4
unnamed: SV4.5, SV4.6
unnamed: SV4.7, SV4.8
unnamed: SV5.7, SV5.8
unnamed: SV4.11, SV4.12
unnamed: SV4.13, SV4.14
unnamed: SV4.15, SV4.16
unnamed: SV4.17, SV4.18
unnamed: SV4.19, SV4.20
unnamed: SV4.21, SV4.22
unnamed: SV4.23, SV4.24
unnamed: SV5.9, SV5.10
unnamed: SV4.27, SV4.28
unnamed: SV4.29, SV4.30
unnamed: SV4.31, SV4.32
unnamed: SV4.33, SV4.34
unnamed: SV4.35, SV4.36
unnamed: SV4.37, SV4.38
unnamed: SV5.11, SV5.12
unnamed: SV2.39, SV2.40
unnamed: SV2.37, SV2.38
unnamed: SV2.35, SV2.36
unnamed: SV6.1, SV6.2
unnamed: SV2.31, SV2.32
unnamed: SV6.3, SV6.4
unnamed: SV2.27, SV2.28
unnamed: SV2.25, SV2.26
unnamed: SV2.23, SV2.24
unnamed: SV2.21, SV2.22
unnamed: SV6.5, SV6.6
unnamed: SV2.17, SV2.18
unnamed: SV2.15, SV2.16
unnamed: SV6.7, SV6.8
unnamed: SV2.11, SV2.12
unnamed: SV2.9, SV2.10
unnamed: SV2.7, SV2.8
unnamed: SV2.5, SV2.6
unnamed: SV6.9, SV6.10
unnamed: SV6.11, SV6.12
unnamed: J70.P$1, J70.P$2
unnamed: J71.P$1, J71.P$2
unnamed: J72.P$1, J72.P$2
unnamed: J73.P$1, J73.P$2
unnamed: J74.P$1, J74.P$2
unnamed: J75.P$1, J75.P$2
unnamed: J76.P$1, J76.P$2
unnamed: J77.P$1, J77.P$2
unnamed: J88.P$2 (R+), J89.P$1, J89.P$2
unnamed: J88.P$5 (R-), J90.P$1, J90.P$2
unnamed: J88.P$1, J91.P$1, J91.P$2
unnamed: J88.P$3, J92.P$1, J92.P$2
unnamed: J88.P$4, J93.P$1, J93.P$2
POWER: B2.P$1 (BAT+); also elsewhere on the board
VCC: J65.P$1, J65.P$2; also elsewhere on the board

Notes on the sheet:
For Pushbuttons

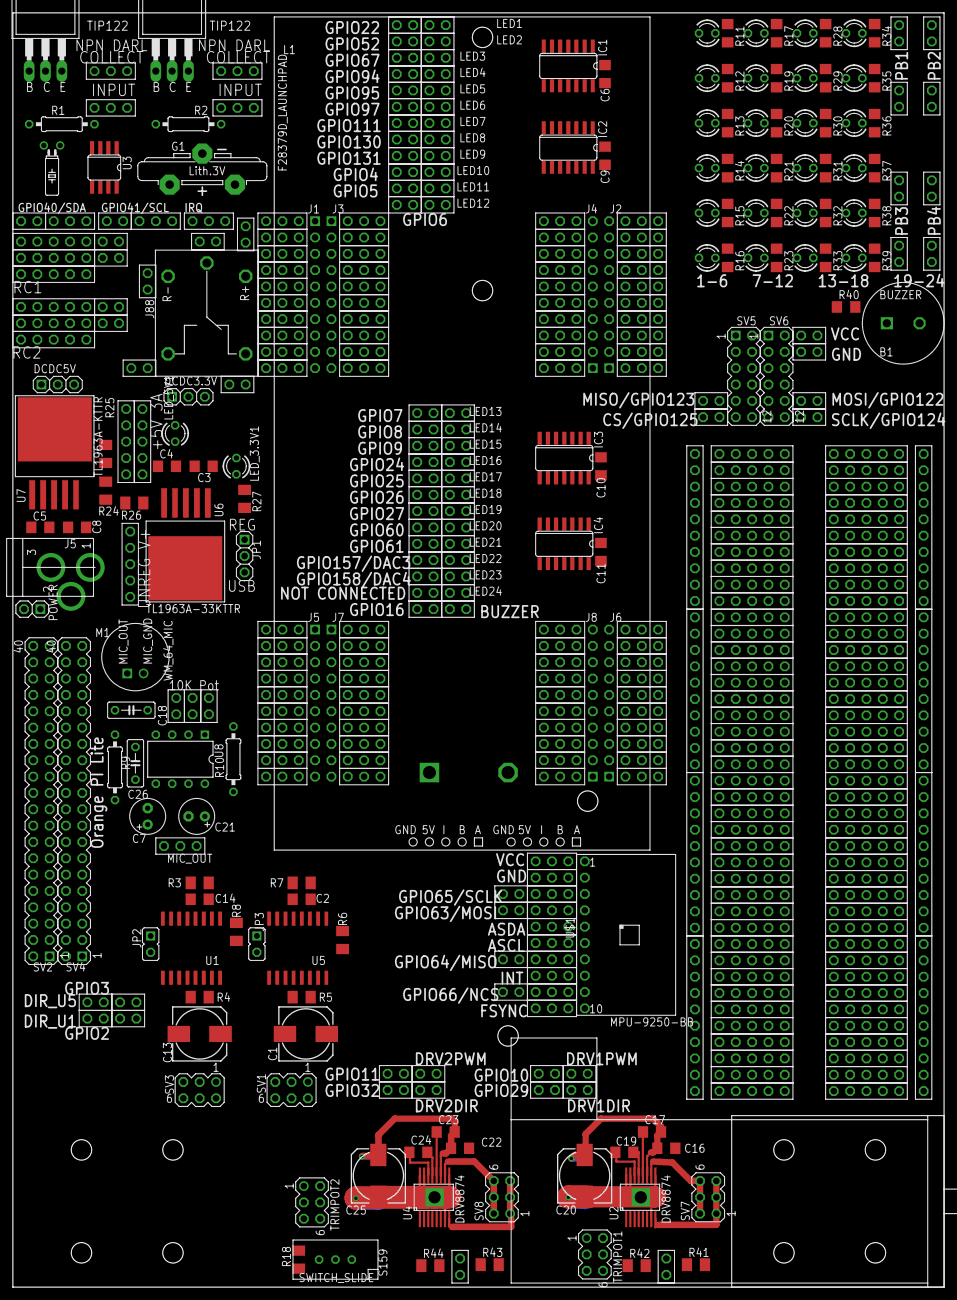
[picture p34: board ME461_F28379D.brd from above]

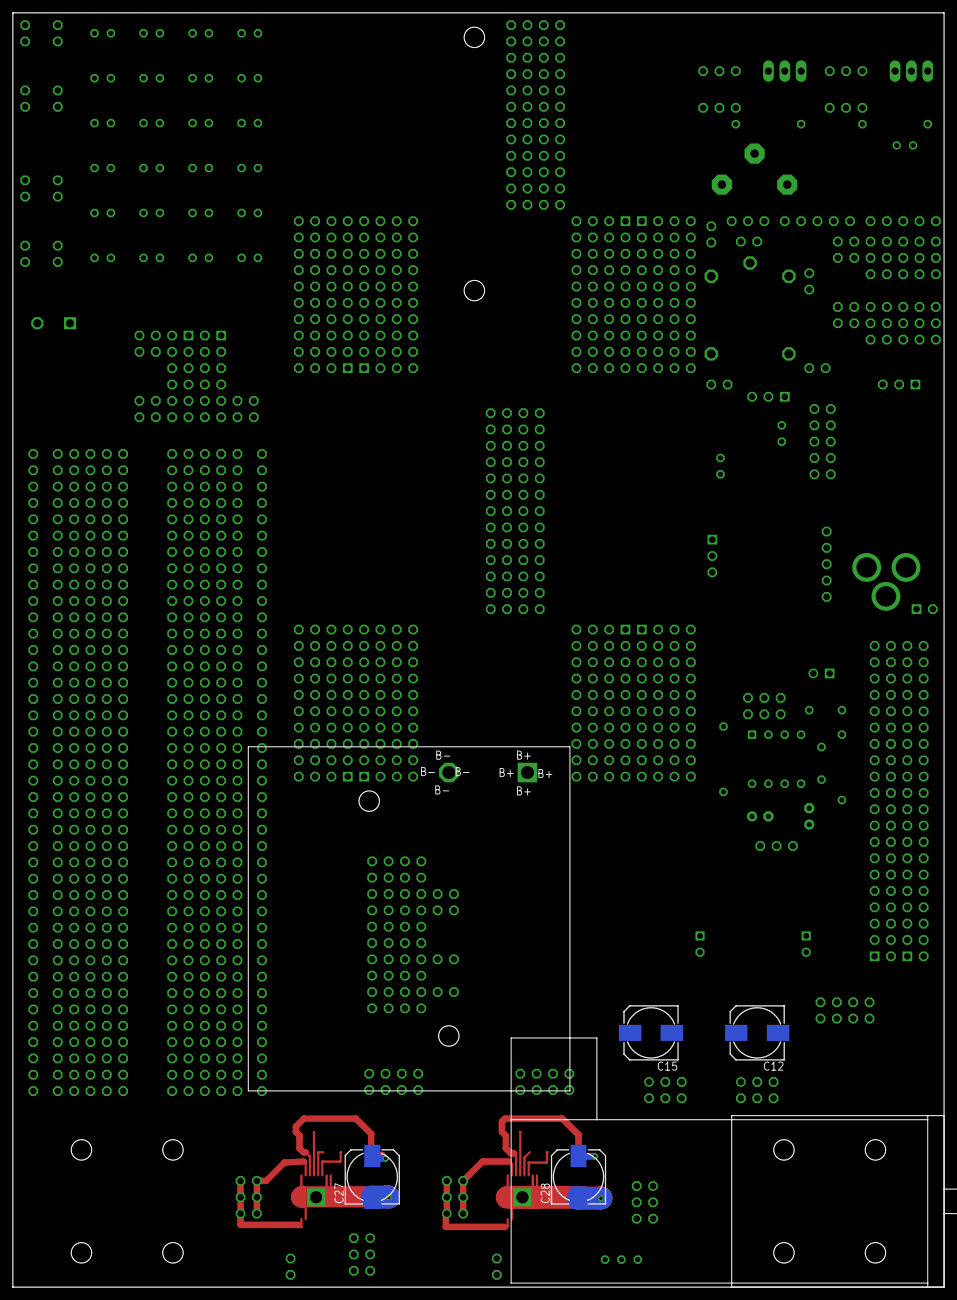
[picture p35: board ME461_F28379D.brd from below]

Board: 2 copper layers, 144.8 x 198.1 mm, 432 parts (6 on the bottom side), 355 nets.

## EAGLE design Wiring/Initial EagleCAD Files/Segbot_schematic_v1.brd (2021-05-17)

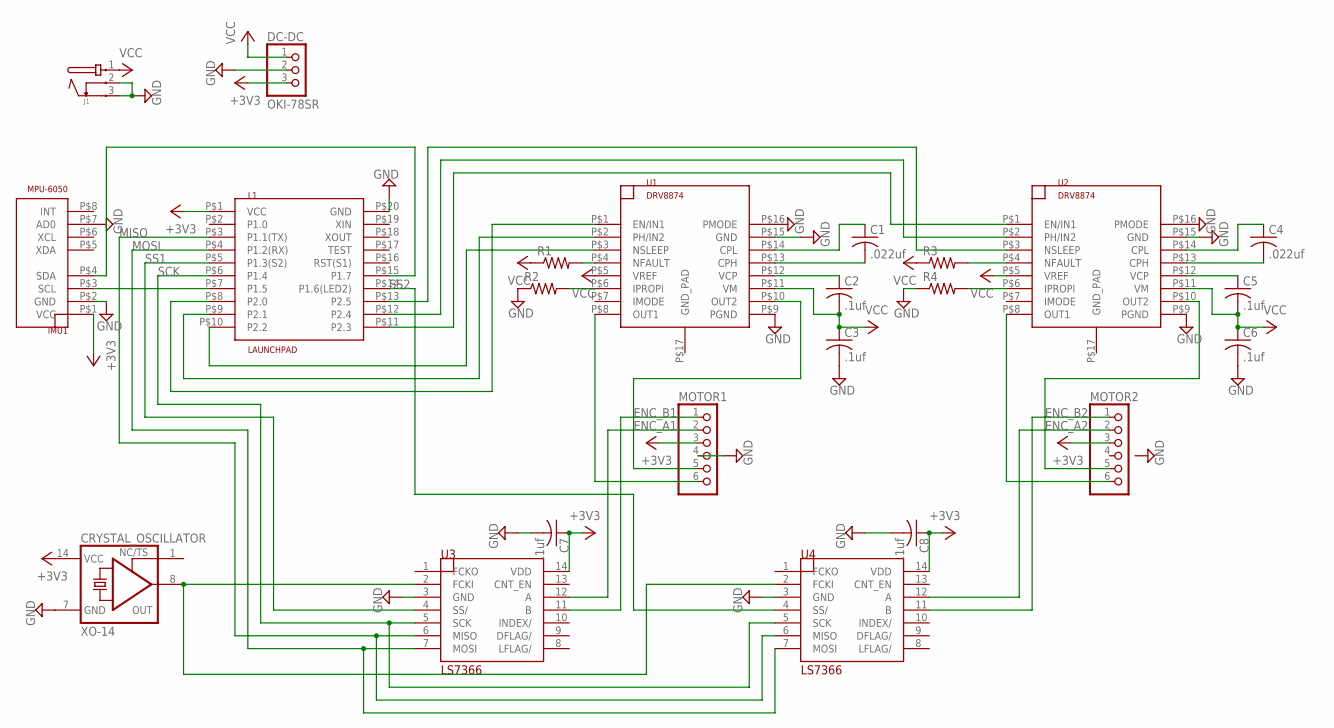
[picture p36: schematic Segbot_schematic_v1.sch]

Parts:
C1, C4: .022uf; C025-024X044
C2, C3, C5, C6: .1uf; C025-024X044
C7, C8: .1uf; C1206
CRYSTAL_OSCILLATOR: XO-14; DIL14S
DC-DC: OKI-78SR; 1X03
IMU1: MPU-6050; MPU6050_MODULE
J1: JACK-PMS
L1: LAUNCHPAD
MOTOR1, MOTOR2: PINHD-1X6; 1X06
R1, R2, R3, R4: R-US_R1206; R1206
U1, U2: DRV8874; HTSSOP16
U3, U4: LS7366; SO14

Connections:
+3V3: C7.1, C8.1, CRYSTAL_OSCILLATOR.14 (VCC), DC-DC.3, IMU1.P$1 (VCC), L1.P$1 (VCC), MOTOR1.3, MOTOR2.3, U3.14 (VDD), U4.14 (VDD)
ENC_A1: MOTOR1.2, U3.12 (A)
ENC_A2: MOTOR2.2, U4.12 (A)
ENC_B1: MOTOR1.1, U3.11 (B)
ENC_B2: MOTOR2.1, U4.11 (B)
GND: C3.2, C6.2, C7.2, C8.2, CRYSTAL_OSCILLATOR.7 (GND), DC-DC.2, IMU1.P$2 (GND), IMU1.P$7 (AD0), J1.2, J1.3, L1.P$20 (GND), MOTOR1.4, R2.1, R4.1, U1.P$9 (PGND), U1.P$15 (GND), U1.P$16 (PMODE), U2.P$9 (PGND), U2.P$15 (GND), U2.P$16 (PMODE), U3.3 (GND), U4.3 (GND)
MISO: L1.P$3 (P1.1(TX)), U3.6 (MISO), U4.6 (MISO)
MOSI: L1.P$4 (P1.2(RX)), U3.7 (MOSI), U4.7 (MOSI)
unnamed: IMU1.P$3 (SCL), L1.P$7 (P1.5)
unnamed: IMU1.P$4 (SDA), L1.P$15 (P1.7)
unnamed: L1.P$8 (P2.0), U1.P$1 (EN/IN1)
unnamed: L1.P$9 (P2.1), U1.P$2 (PH/IN2)
unnamed: L1.P$10 (P2.2), U1.P$3 (NSLEEP)
unnamed: R1.2, U1.P$4 (NFAULT)
unnamed: R2.2, U1.P$6 (IPROPI)
unnamed: C1.1, U1.P$14 (CPL)
unnamed: C1.2, U1.P$13 (CPH)
unnamed: C2.1, U1.P$12 (VCP)
unnamed: MOTOR1.6, U1.P$8 (OUT1)
unnamed: MOTOR1.5, U1.P$10 (OUT2)
unnamed: L1.P$11 (P2.3), U2.P$1 (EN/IN1)
unnamed: L1.P$12 (P2.4), U2.P$2 (PH/IN2)
unnamed: L1.P$13 (P2.5), U2.P$3 (NSLEEP)
unnamed: C4.1, U2.P$14 (CPL)
unnamed: C4.2, U2.P$13 (CPH)
unnamed: C5.1, U2.P$12 (VCP)
unnamed: R3.2, U2.P$4 (NFAULT)
unnamed: R4.2, U2.P$6 (IPROPI)
unnamed: MOTOR2.6, U2.P$8 (OUT1)
unnamed: MOTOR2.5, U2.P$10 (OUT2)
unnamed: CRYSTAL_OSCILLATOR.8 (OUT), U3.2 (FCKI), U4.2 (FCKI)
SCK: L1.P$6 (P1.4), U3.5 (SCK), U4.5 (SCK)
SS1: L1.P$5 (P1.3(S2)), U3.4 (SS/)
SS2: L1.P$14 (P1.6(LED2)), U4.4 (SS/)
VCC: C2.2, C3.1, C5.2, C6.1, DC-DC.1, J1.1, R1.1, R3.1, U1.P$5 (VREF), U1.P$11 (VM), U2.P$5 (VREF), U2.P$11 (VM)

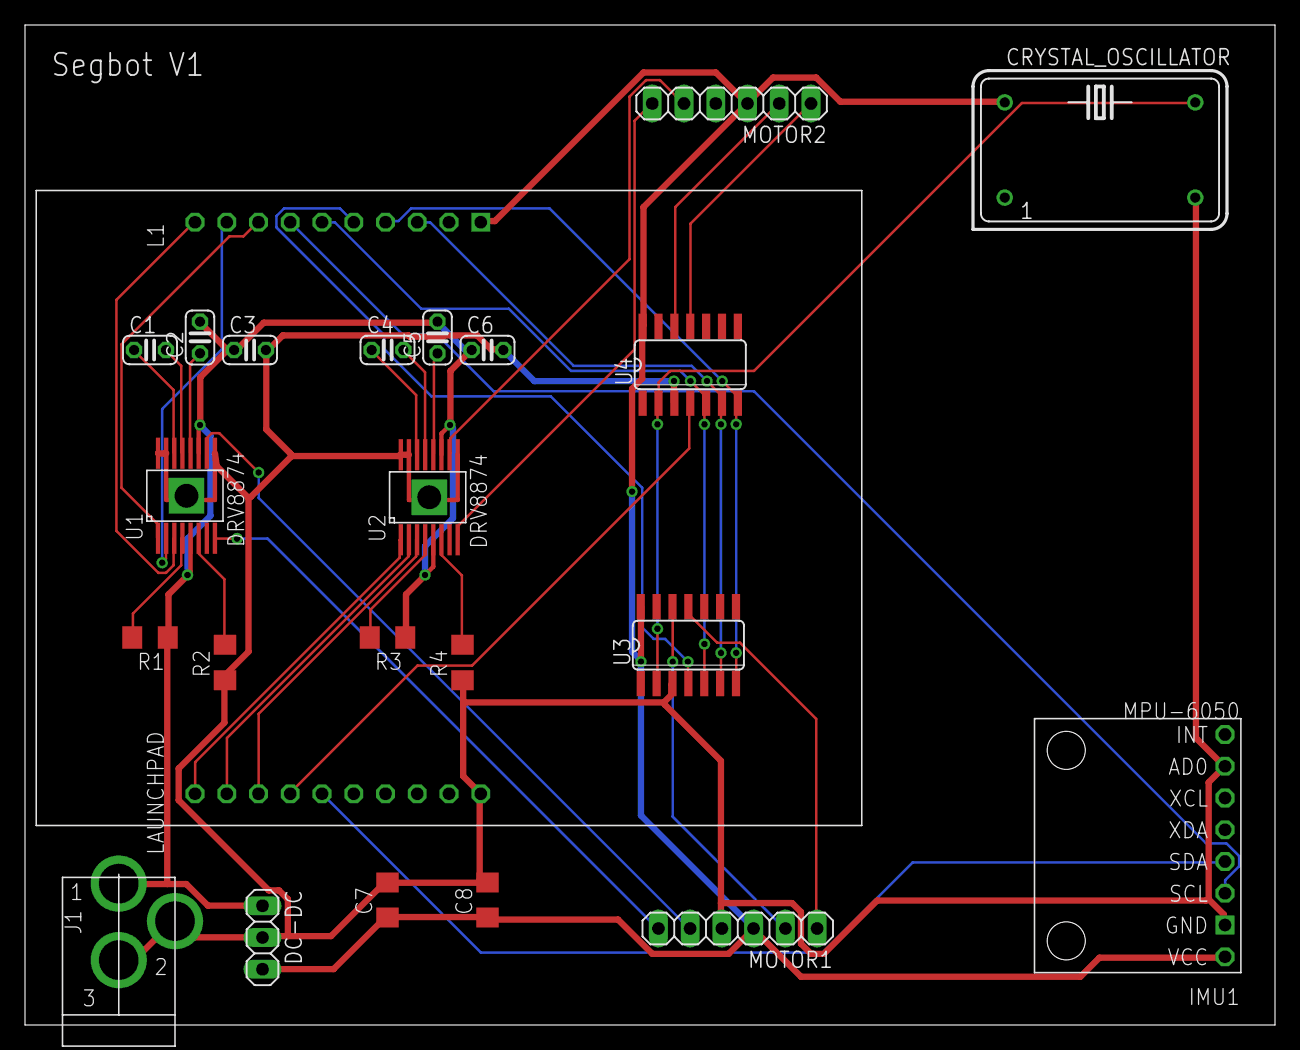
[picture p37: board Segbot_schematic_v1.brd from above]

Board: 2 copper layers, 100.0 x 80.0 mm, 23 parts (0 on the bottom side), 35 nets.

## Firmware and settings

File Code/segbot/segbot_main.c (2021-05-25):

//#############################################################################
// FILE:   segbot_main.c
//
// TITLE:  Segbot
//#############################################################################

// Included Files
#include <stdio.h>
#include <stdlib.h>
#include <stdarg.h>
#include <string.h>
#include <math.h>
#include <limits.h>
#include "F28x_Project.h"
#include "driverlib.h"
#include "device.h"
#include "f28379dSerial.h"

#define PI          3.1415926535897932384626433832795
#define TWOPI       6.283185307179586476925286766559
#define HALFPI      1.5707963267948966192313216916398

// PREDEFINITIONS ----------------------------------------------------------------------------------------------------------------------
__interrupt void cpu_timer0_isr(void);
__interrupt void cpu_timer1_isr(void);
__interrupt void cpu_timer2_isr(void);
__interrupt void SWI_isr(void);
float readEncLeft(void);
float readEncRight(void);
void setEPWM6A(float);
void setEPWM6B(float);
void setDACA(float);
void setDACB(float);
__interrupt void ADCA_ISR(void);
__interrupt void SPIB_isr(void);
void init_eQEPs(void);
void setupEPWM5(void);
void setupADC(void);
void setupDAC(void);
void setupSpib(void);
void serialRXA(serial_t *s, char data);

// VARIABLES ---------------------------------------------------------------------------------------------------------------------------
uint32_t numTimer0calls = 0;
uint32_t numSWIcalls = 0;
uint32_t numRXA = 0;
uint16_t UARTPrint = 0;
uint32_t SPIB_isr_count = 0;
// joystick readings
float adcina2Volts = 0;  // ADCINA2 is connected to pin 29 = VRX = LR
float adcina3Volts = 0;  // ADCINA3 is connected to pin 26 = VRY = UD
// MPU-9250 readings
float accelXreading = 0, accelYreading = 0, accelZreading = 0;
float gyroXreading = 0, gyroYreading = 0, gyroZreading = 0;
// wheel info
float leftWheel = 0, leftWheelPrev = 0;
float rightWheel = 0, rightWheelPrev = 0;
// control algorithm
float uLeft = 0, uRight = 0;
float K1 = -34.3159*(10.0/6.0), K2 = -3.6375*(10.0/6.0), K3 = -3.3290*(10.0/6.0);       // -30, -2.8, -1.0
float leftVel = 0, leftVelPrev = 0;
float rightVel = 0, rightVelPrev = 0;
float ubal = 0;
float wheelDiff = 0, wheelDiffPrev = 0;
float wheelDiffVel = 0, wheelDiffVelPrev = 0;
// turning
float turnRef = 0, turnRefPrev = 0;
float turnRate = 0, turnRatePrev = 0;
float turnError = 0, turnErrorPrev = 0;
float turnErrorInt = 0, turnErrorIntPrev = 0;
float turn = 0;     // positive is left, negative is right
float FwdBackOffset = 0;
float Kp = 3.0, Ki = 20.0, Kd = 0.08;       // 3.0, 20.0, 0.08
// variables for calibrating and finding the balancing point
float accelx_offset = 0, accely_offset = 0, accelz_offset = 0;
float gyrox_offset = 0, gyroy_offset = 0, gyroz_offset = 0;
float accelzBalancePoint = -.83;        // -.76
int16 IMU_data[9];
uint16_t temp=0;
int16_t doneCal = 0;
float tilt_value = 0;
float tilt_array[4] = {0, 0, 0, 0};
float gyro_value = 0;
float gyro_array[4] = {0, 0, 0, 0};
float LeftWheelArray[4] = {0,0,0,0};
float RightWheelArray[4] = {0,0,0,0};
// Kalman Filter vars
float T = 0.001; //sample rate, 1ms
float Q = 0.01; // made global to enable changing in runtime
float R = 25000;//50000;
float kalman_tilt = 0;
float kalman_P = 22.365;
int16_t SpibNumCalls = -1;
float pred_P = 0;
float kalman_K = 0;
int32_t timecount = 0;
int16_t calibration_state = 0;
int32_t calibration_count = 0;

void main(void) {
    // PLL, WatchDog, enable Peripheral Clocks
    // This example function is found in the F2837xD_SysCtrl.c file.
    InitSysCtrl();
    InitGpio();

    // Blue LED on LuanchPad
    GPIO_SetupPinMux(31, GPIO_MUX_CPU1, 0);
    GPIO_SetupPinOptions(31, GPIO_OUTPUT, GPIO_PUSHPULL);
    GpioDataRegs.GPASET.bit.GPIO31 = 1;

    // Red LED on LaunchPad
    GPIO_SetupPinMux(34, GPIO_MUX_CPU1, 0);
    GPIO_SetupPinOptions(34, GPIO_OUTPUT, GPIO_PUSHPULL);
    GpioDataRegs.GPBSET.bit.GPIO34 = 1;

    // LED1 and PWM Pin
    GPIO_SetupPinMux(22, GPIO_MUX_CPU1, 0);
    GPIO_SetupPinOptions(22, GPIO_OUTPUT, GPIO_PUSHPULL);
    GpioDataRegs.GPACLEAR.bit.GPIO22 = 1;

    // LED2
    GPIO_SetupPinMux(52, GPIO_MUX_CPU1, 0);
    GPIO_SetupPinOptions(52, GPIO_OUTPUT, GPIO_PUSHPULL);
    GpioDataRegs.GPBCLEAR.bit.GPIO52 = 1;

    // LED3
    GPIO_SetupPinMux(67, GPIO_MUX_CPU1, 0);
    GPIO_SetupPinOptions(67, GPIO_OUTPUT, GPIO_PUSHPULL);
    GpioDataRegs.GPCCLEAR.bit.GPIO67 = 1;

    // LED4
    GPIO_SetupPinMux(94, GPIO_MUX_CPU1, 0);
    GPIO_SetupPinOptions(94, GPIO_OUTPUT, GPIO_PUSHPULL);
    GpioDataRegs.GPCCLEAR.bit.GPIO94 = 1;

    // LED5
    GPIO_SetupPinMux(95, GPIO_MUX_CPU1, 0);
    GPIO_SetupPinOptions(95, GPIO_OUTPUT, GPIO_PUSHPULL);
    GpioDataRegs.GPCCLEAR.bit.GPIO95 = 1;

    // LED6
    GPIO_SetupPinMux(97, GPIO_MUX_CPU1, 0);
    GPIO_SetupPinOptions(97, GPIO_OUTPUT, GPIO_PUSHPULL);
    GpioDataRegs.GPDCLEAR.bit.GPIO97 = 1;

    // LED7
    GPIO_SetupPinMux(111, GPIO_MUX_CPU1, 0);
    GPIO_SetupPinOptions(111, GPIO_OUTPUT, GPIO_PUSHPULL);
    GpioDataRegs.GPDCLEAR.bit.GPIO111 = 1;

    // LED8
    GPIO_SetupPinMux(130, GPIO_MUX_CPU1, 0);
    GPIO_SetupPinOptions(130, GPIO_OUTPUT, GPIO_PUSHPULL);
    GpioDataRegs.GPECLEAR.bit.GPIO130 = 1;

    // LED9
    GPIO_SetupPinMux(131, GPIO_MUX_CPU1, 0);
    GPIO_SetupPinOptions(131, GPIO_OUTPUT, GPIO_PUSHPULL);
    GpioDataRegs.GPECLEAR.bit.GPIO131 = 1;

    // LED10
    GPIO_SetupPinMux(4, GPIO_MUX_CPU1, 0);
    GPIO_SetupPinOptions(4, GPIO_OUTPUT, GPIO_PUSHPULL);
    GpioDataRegs.GPACLEAR.bit.GPIO4 = 1;

    // LED11
    GPIO_SetupPinMux(5, GPIO_MUX_CPU1, 0);
    GPIO_SetupPinOptions(5, GPIO_OUTPUT, GPIO_PUSHPULL);
    GpioDataRegs.GPACLEAR.bit.GPIO5 = 1;

    // LED12
    GPIO_SetupPinMux(6, GPIO_MUX_CPU1, 0);
    GPIO_SetupPinOptions(6, GPIO_OUTPUT, GPIO_PUSHPULL);
    GpioDataRegs.GPACLEAR.bit.GPIO6 = 1;

    // LED13
    GPIO_SetupPinMux(7, GPIO_MUX_CPU1, 0);
    GPIO_SetupPinOptions(7, GPIO_OUTPUT, GPIO_PUSHPULL);
    GpioDataRegs.GPACLEAR.bit.GPIO7 = 1;

    // LED14
    GPIO_SetupPinMux(8, GPIO_MUX_CPU1, 0);
    GPIO_SetupPinOptions(8, GPIO_OUTPUT, GPIO_PUSHPULL);
    GpioDataRegs.GPACLEAR.bit.GPIO8 = 1;

    // LED15
    GPIO_SetupPinMux(9, GPIO_MUX_CPU1, 0);
    GPIO_SetupPinOptions(9, GPIO_OUTPUT, GPIO_PUSHPULL);
    GpioDataRegs.GPACLEAR.bit.GPIO9 = 1;

    // LED16
    GPIO_SetupPinMux(24, GPIO_MUX_CPU1, 0);
    GPIO_SetupPinOptions(24, GPIO_OUTPUT, GPIO_PUSHPULL);
    GpioDataRegs.GPACLEAR.bit.GPIO24 = 1;

    // LED17
    GPIO_SetupPinMux(25, GPIO_MUX_CPU1, 0);
    GPIO_SetupPinOptions(25, GPIO_OUTPUT, GPIO_PUSHPULL);
    GpioDataRegs.GPACLEAR.bit.GPIO25 = 1;

    // LED18
    GPIO_SetupPinMux(26, GPIO_MUX_CPU1, 0);
    GPIO_SetupPinOptions(26, GPIO_OUTPUT, GPIO_PUSHPULL);
    GpioDataRegs.GPACLEAR.bit.GPIO26 = 1;

    // LED19
    GPIO_SetupPinMux(27, GPIO_MUX_CPU1, 0);
    GPIO_SetupPinOptions(27, GPIO_OUTPUT, GPIO_PUSHPULL);
    GpioDataRegs.GPACLEAR.bit.GPIO27 = 1;

    // LED20
    GPIO_SetupPinMux(60, GPIO_MUX_CPU1, 0);
    GPIO_SetupPinOptions(60, GPIO_OUTPUT, GPIO_PUSHPULL);
    GpioDataRegs.GPBCLEAR.bit.GPIO60 = 1;

    // LED21
    GPIO_SetupPinMux(61, GPIO_MUX_CPU1, 0);
    GPIO_SetupPinOptions(61, GPIO_OUTPUT, GPIO_PUSHPULL);
    GpioDataRegs.GPBCLEAR.bit.GPIO61 = 1;

    // LED22
    GPIO_SetupPinMux(157, GPIO_MUX_CPU1, 0);
    GPIO_SetupPinOptions(157, GPIO_OUTPUT, GPIO_PUSHPULL);
    GpioDataRegs.GPECLEAR.bit.GPIO157 = 1;

    // LED23
    GPIO_SetupPinMux(158, GPIO_MUX_CPU1, 0);
    GPIO_SetupPinOptions(158, GPIO_OUTPUT, GPIO_PUSHPULL);
    GpioDataRegs.GPECLEAR.bit.GPIO158 = 1;

    //DRV8874 #1 DIR  Direction
    GPIO_SetupPinMux(29, GPIO_MUX_CPU1, 0);
    GPIO_SetupPinOptions(29, GPIO_OUTPUT, GPIO_PUSHPULL);
    GpioDataRegs.GPASET.bit.GPIO29 = 1;

    //DRV8874 #2 DIR  Direction
    GPIO_SetupPinMux(32, GPIO_MUX_CPU1, 0);
    GPIO_SetupPinOptions(32, GPIO_OUTPUT, GPIO_PUSHPULL);
    GpioDataRegs.GPBSET.bit.GPIO32 = 1;

    //MPU9250  CS  Chip Select
    GPIO_SetupPinMux(66, GPIO_MUX_CPU1, 0);
    GPIO_SetupPinOptions(66, GPIO_OUTPUT, GPIO_PUSHPULL);
    GpioDataRegs.GPCSET.bit.GPIO66 = 1;

    //PushButton 1
    GPIO_SetupPinMux(122, GPIO_MUX_CPU1, 0);
    GPIO_SetupPinOptions(122, GPIO_INPUT, GPIO_PULLUP);

    //PushButton 2
    GPIO_SetupPinMux(123, GPIO_MUX_CPU1, 0);
    GPIO_SetupPinOptions(123, GPIO_INPUT, GPIO_PULLUP);

    //PushButton 3
    GPIO_SetupPinMux(124, GPIO_MUX_CPU1, 0);
    GPIO_SetupPinOptions(124, GPIO_INPUT, GPIO_PULLUP);

    //PushButton 4
    GPIO_SetupPinMux(125, GPIO_MUX_CPU1, 0);
    GPIO_SetupPinOptions(125, GPIO_INPUT, GPIO_PULLUP);

    // Clear all interrupts and initialize PIE vector table:
    // Disable CPU interrupts
    DINT;

    // My setup functions
    setupSpib();
    init_eQEPs();

    // Initialize the PIE control registers to their default state.
    // The default state is all PIE interrupts disabled and flags
    // are cleared.
    // This function is found in the F2837xD_PieCtrl.c file.
    InitPieCtrl();

    // Disable CPU interrupts and clear all CPU interrupt flags:
    IER = 0x0000;
    IFR = 0x0000;

    // Initialize the PIE vector table with pointers to the shell Interrupt
    // Service Routines (ISR).
    // This will populate the entire table, even if the interrupt
    // is not used in this example.  This is useful for debug purposes.
    // The shell ISR routines are found in F2837xD_DefaultIsr.c.
    // This function is found in F2837xD_PieVect.c.
    InitPieVectTable();

    // Interrupts that are used in this example are re-mapped to
    // ISR functions found within this project
    EALLOW;  // This is needed to write to EALLOW protected registers
    PieVectTable.TIMER0_INT = &cpu_timer0_isr;
    PieVectTable.TIMER1_INT = &cpu_timer1_isr;
    PieVectTable.TIMER2_INT = &cpu_timer2_isr;
    PieVectTable.SCIA_RX_INT = &RXAINT_recv_ready;
    PieVectTable.SCIC_RX_INT = &RXCINT_recv_ready;
    PieVectTable.SCID_RX_INT = &RXDINT_recv_ready;
    PieVectTable.SCIA_TX_INT = &TXAINT_data_sent;
    PieVectTable.SCIC_TX_INT = &TXCINT_data_sent;
    PieVectTable.SCID_TX_INT = &TXDINT_data_sent;
    PieVectTable.ADCA1_INT = &ADCA_ISR;     // tells processor to call ADCA_ISR when ADCA2 interrupt occurs

    PieVectTable.EMIF_ERROR_INT = &SWI_isr;
    PieVectTable.SPIB_RX_INT = &SPIB_isr;       // ex2, q3, part b
    EDIS;    // This is needed to disable write to EALLOW protected registers

    // More of my setup functions
    setupEPWM5();       // Setup EPWM5 to be a timer to trigger ADCD conversion sequence
    setupADC();     // Setup SOC0 and SOC1 to trigger
    setupDAC();     // Enable DACA and DACB outputs

    // Initialize the CpuTimers Device Peripheral. This function can be
    // found in F2837xD_CpuTimers.c
    InitCpuTimers();

    // Configure CPU-Timer 0, 1, and 2 to interrupt every second:
    // 200MHz CPU Freq, 1 second Period (in uSeconds)
    ConfigCpuTimer(&CpuTimer0, 200, 1000);     // 1,000us = 1ms = 0.001s
    ConfigCpuTimer(&CpuTimer1, 200, 4000);     // 4,000us = 4ms = 0.004s
    ConfigCpuTimer(&CpuTimer2, 200, 40000);

    // Enable CpuTimer Interrupt bit TIE
    CpuTimer0Regs.TCR.all = 0x4000;
    CpuTimer1Regs.TCR.all = 0x4000;
    CpuTimer2Regs.TCR.all = 0x4000;

    init_serial(&SerialA,115200,serialRXA);
//    init_serial(&SerialC,115200,serialRXC);
//    init_serial(&SerialD,115200,serialRXD);

    // Enable CPU int1 which is connected to CPU-Timer 0, CPU int13
    // which is connected to CPU-Timer 1, and CPU int 14, which is connected
    // to CPU-Timer 2:  int 12 is for the SWI.
    IER |= M_INT1;
    IER |= M_INT8;  // SCIC SCID
    IER |= M_INT9;  // SCIA
    IER |= M_INT12;
    IER |= M_INT13;
    IER |= M_INT14;
    IER |= M_INT6;      // SPIB_RX

    // Enable TINT0 in the PIE: Group 1 interrupt 7
    PieCtrlRegs.PIEIER1.bit.INTx7 = 1;
    // Enable SWI in the PIE: Group 12 interrupt 9
    PieCtrlRegs.PIEIER12.bit.INTx9 = 1;
    // Enables PIE interrupt 1.1
    PieCtrlRegs.PIEIER1.bit.INTx1 = 1;      // ADCA1, Table3-2 in ADC technical reference
    // Enable SPIB_RX interrupt: 6.3
    PieCtrlRegs.PIEIER6.bit.INTx3 = 1;

    // setup EPWM6A and B with 20kHz carrier frequency
    EALLOW;
    EPwm6Regs.TBCTL.bit.CTRMODE = 0x0;     // Up-count mode
    EPwm6Regs.TBCTL.bit.FREE_SOFT = 0x2;      // Free run; 1x means use any value that isn't already in use
    EPwm6Regs.TBCTL.bit.PHSEN = 0x0;       // disable phase loading
    EPwm6Regs.TBCTL.bit.CLKDIV = 0x0;      // clock divide to 1
    EPwm6Regs.TBCTR = 0;     // start timers at zero
    EPwm6Regs.TBPRD = 2500;     // (1/20,000)/(1/50,000,000) = 2500 b/c main clock ctr is 50MHz and prd here is 20KHz
    EPwm6Regs.CMPA.bit.CMPA = 0;    // start duty cycle at 0%
    EPwm6Regs.CMPB.bit.CMPB = 0;
    EPwm6Regs.AQCTLA.bit.CAU = 0x1;    // when TBCTR = CMPB on up count, clear (force EPWMxA output low)
    EPwm6Regs.AQCTLB.bit.CBU = 0x1;
    EPwm6Regs.AQCTLA.bit.ZRO = 0x2;    // when TBCTR = 0, set high
    EPwm6Regs.AQCTLB.bit.ZRO = 0x2;
    EPwm6Regs.TBPHS.bit.TBPHS = 0;     // set phase to zero
    EDIS;
    GPIO_SetupPinMux(10, GPIO_MUX_CPU1, 1);     // set DRV1PWM from GPIO10 to EPWM6A
    GPIO_SetupPinMux(11, GPIO_MUX_CPU1, 1);     // set DRV2PWM from GPIO11 to EPWM6B

    EALLOW;
    GpioCtrlRegs.GPAPUD.bit.GPIO10 = 1;
    GpioCtrlRegs.GPAPUD.bit.GPIO11 = 1;
    EDIS;

    // Enable global Interrupts and higher priority real-time debug events
    EINT;  // Enable Global interrupt INTM
    ERTM;  // Enable Global realtime interrupt DBGM

    // IDLE loop. Just sit and loop forever (optional):
    while(1) {
        if (UARTPrint == 1 ) {
                //serial_printf(&SerialA,"wheels: (%.3f, %.3f) gyro: (%.3f, %.3f, %.3f) accel:(%.3f, %.3f, %.3f)\r\n", leftWheel, rightWheel, gyroXreading, gyroYreading, gyroZreading, accelXreading, accelYreading, accelZreading);
            serial_printf(&SerialA,"tilt_value: %.3f, gyro_value: %.3f, wheel vel: (%.3f, %.3f)\r\n", tilt_value, gyro_value, leftWheel, rightWheel);
            UARTPrint = 0;
        }
    }
}

// HELPER FUNCTIONS -----------------------------------------------------------------------------------------------------------------------

float readEncLeft(void) {
    int32_t raw = 0;
    uint32_t QEP_maxvalue = 0xFFFFFFFFU; //4294967295U
    raw = EQep1Regs.QPOSCNT;
    if (raw >= QEP_maxvalue/2) raw -= QEP_maxvalue; // I don't think this is needed and never true
    // 20 North South magnet poles in the encoder disk so 20 square waves per one revolution of the
    // DC motor's back shaft. Then Quadrature Decoder mode multiplies this by 4 so 80 counts per one rev
    // of the DC motor's back shaft. Then the gear motor's gear ratio is 18.7.
    return (raw*(-TWOPI/(80*18.7)));
}

float readEncRight(void) {
    int32_t raw = 0;
    uint32_t QEP_maxvalue = 0xFFFFFFFFU; //4294967295U -1 32bit signed int
    raw = EQep2Regs.QPOSCNT;
    if (raw >= QEP_maxvalue/2) raw -= QEP_maxvalue; // I don't think this is needed and never true
    // 20 North South magnet poles in the encoder disk so 20 square waves per one revolution of the
    // DC motor's back shaft. Then Quadrature Decoder mode multiplies this by 4 so 80 counts per one rev
    // of the DC motor's back shaft. Then the gear motor's gear ratio is 18.7.
    return (raw*(TWOPI/(80*18.7)));
}

void setEPWM6A(float controleffort) {       // LEFT WHEEL
    controleffort = -controleffort;     // so that a positive u spins the wheels forwards
    // set control effort range
    if (controleffort > 10) controleffort = 10;
    if (controleffort < -10) controleffort = -10;

    // there was an issue when testing my board where the motor's pinout was different on the right wheel so the code here for forward and backwards are swapped
    if (controleffort >= 0) GpioDataRegs.GPACLEAR.bit.GPIO29 = 1;    // if positive control effort, turn wheel forwards
    else GpioDataRegs.GPASET.bit.GPIO29 = 1;       // if negative control effort, turn wheel backwards

    EPwm6Regs.CMPA.bit.CMPA = (fabs(controleffort) /10.0) * EPwm6Regs.TBPRD;        // scales control effort to period and set for duty cycle
}

void setEPWM6B(float controleffort) {       // RIGHT WHEEL
    controleffort = -controleffort;     // so that a positive u spins the wheel forwards
    // set control effort range
    if (controleffort > 10) controleffort = 10;
    if (controleffort < -10) controleffort = -10;

    if (controleffort >= 0) GpioDataRegs.GPBSET.bit.GPIO32 = 1;    // if positive control effort, turn wheel forwards
    else GpioDataRegs.GPBCLEAR.bit.GPIO32 = 1;       // if negative control effort, turn wheel backwards

    EPwm6Regs.CMPB.bit.CMPB = (fabs(controleffort) /10.0) * EPwm6Regs.TBPRD;        // scales control effort to period and set for duty cycle
}

void setDACA(float dacouta0) {
    if (dacouta0 > 3.0) dacouta0 = 3.0;
    if (dacouta0 < 0.0) dacouta0 = 0.0;
    DacaRegs.DACVALS.bit.DACVALS = (int)(dacouta0/3.0 * 4095); // perform scaling of 0-3 to 0-4095
}

void setDACB(float dacouta1) {
    if (dacouta1 > 3.0) dacouta1 = 3.0;
    if (dacouta1 < 0.0) dacouta1 = 0.0;
    DacbRegs.DACVALS.bit.DACVALS = (int)(dacouta1/3.0 * 4095); // perform scaling of 0-3 to 0-4095
}

// INTERRUPT SERVICE ROUTINES AND RX TX BUFFERS -------------------------------------------------------------------------------------------

// ADCA hardware interrupt, called every 1ms
__interrupt void ADCA_ISR(void) {
    GpioDataRegs.GPBSET.bit.GPIO52 = 1;

    // JOYSTICK READINGS
    float adca2out = AdcaResultRegs.ADCRESULT0;       // ADCINA2 is connected to pin 29 = VRX = LR
    float adca3out = AdcaResultRegs.ADCRESULT1;       // ADCINA3 is connected to pin 26 = VRY = UD
    adcina2Volts = adca2out * (3.0/4095.0);
    adcina3Volts = adca3out * (3.0/4095.0);

    // IMU READINGS
    GpioDataRegs.GPCCLEAR.bit.GPIO66 = 1;       // GPIO66 low to act as slave select
    SpibRegs.SPIFFRX.bit.RXFFIL = 8;        // issue the SPIB_RX_INT when all values are in RX FIFO
    // get accel readings
    SpibRegs.SPITXBUF =  ((0x8000) | (0x3A00));      // read = 0x8000, register = 0x3A00 = INT_STATUS start
    SpibRegs.SPITXBUF = 0;      // full 16 bits of ACCEL_XOUT
    SpibRegs.SPITXBUF = 0;      // full 16 bits of ACCEL_YOUT
    SpibRegs.SPITXBUF = 0;      // full 16 bits of ACCEL_ZOUT
    SpibRegs.SPITXBUF = 0;      // temp
    // get gyro readings
    SpibRegs.SPITXBUF = 0;      // full 16 bits of GYRO_XOUT
    SpibRegs.SPITXBUF = 0;      // full 16 bits of GYRO_YOUT
    SpibRegs.SPITXBUF = 0;      // full 16 bits of GYRO_ZOUT

    // CLEAR INTERRUPT FLAG
    AdcaRegs.ADCINTFLGCLR.bit.ADCINT1 = 1;
    PieCtrlRegs.PIEACK.all = PIEACK_GROUP1;
    GpioDataRegs.GPBCLEAR.bit.GPIO52 = 1;
}
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

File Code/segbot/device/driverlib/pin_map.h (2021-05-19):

//###########################################################################
//
// FILE:   pin_map.h
//
// TITLE:  Definitions of pin mux info for gpio.c.
//
//###########################################################################
// $TI Release: F2837xD Support Library v3.10.00.00 $
// $Release Date: Tue May 26 17:13:46 IST 2020 $
// $Copyright:
// Copyright (C) 2013-2020 Texas Instruments Incorporated - http://www.ti.com/
//
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
//   Redistributions of source code must retain the above copyright 
//   notice, this list of conditions and the following disclaimer.
// 
//   Redistributions in binary form must reproduce the above copyright
//   notice, this list of conditions and the following disclaimer in the 
//   documentation and/or other materials provided with the   
//   distribution.
// 
//   Neither the name of Texas Instruments Incorporated nor the names of
//   its contributors may be used to endorse or promote products derived
//   from this software without specific prior written permission.
// 
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
#ifndef PIN_MAP_H
#define PIN_MAP_H
                                                                               
//*****************************************************************************
// 0x00000003 = MUX register value                                             
// 0x0000000C = GMUX register value                                            
// 0x0000FF00 = Shift amount within mux registers                              
// 0xFFFF0000 = Offset of MUX register                                         
//*****************************************************************************

//*****************************************************************************
// Latest pinmuxing MACROS - Recommended for new users                         
//*****************************************************************************
#define GPIO_0_GPIO0                    0x00060000U
#define GPIO_0_EPWM1A                   0x00060001U
#define GPIO_0_SDAA                     0x00060006U

#define GPIO_1_GPIO1                    0x00060200U
#define GPIO_1_EPWM1B                   0x00060201U
#define GPIO_1_MFSRB                    0x00060203U
#define GPIO_1_SCLA                     0x00060206U

#define GPIO_2_GPIO2                    0x00060400U
#define GPIO_2_EPWM2A                   0x00060401U
#define GPIO_2_OUTPUTXBAR1              0x00060405U
#define GPIO_2_SDAB                     0x00060406U

#define GPIO_3_GPIO3                    0x00060600U
#define GPIO_3_EPWM2B                   0x00060601U
#define GPIO_3_OUTPUTXBAR2              0x00060602U
#define GPIO_3_MCLKRB                   0x00060603U
#define GPIO_3_SCLB                     0x00060606U

#define GPIO_4_GPIO4                    0x00060800U
#define GPIO_4_EPWM3A                   0x00060801U
#define GPIO_4_OUTPUTXBAR3              0x00060805U
#define GPIO_4_CANTXA                   0x00060806U

#define GPIO_5_GPIO5                    0x00060A00U
#define GPIO_5_EPWM3B                   0x00060A01U
#define GPIO_5_MFSRA                    0x00060A02U
#define GPIO_5_OUTPUTXBAR3              0x00060A03U
#define GPIO_5_CANRXA                   0x00060A06U

#define GPIO_6_GPIO6                    0x00060C00U
#define GPIO_6_EPWM4A                   0x00060C01U
#define GPIO_6_OUTPUTXBAR4              0x00060C02U
#define GPIO_6_EPWMSYNCO                0x00060C03U
#define GPIO_6_EQEP3A                   0x00060C05U
#define GPIO_6_CANTXB                   0x00060C06U

#define GPIO_7_GPIO7                    0x00060E00U
#define GPIO_7_EPWM4B                   0x00060E01U
#define GPIO_7_MCLKRA                   0x00060E02U
#define GPIO_7_OUTPUTXBAR5              0x00060E03U
#define GPIO_7_EQEP3B                   0x00060E05U
#define GPIO_7_CANRXB                   0x00060E06U

#define GPIO_8_GPIO8                    0x00061000U
#define GPIO_8_EPWM5A                   0x00061001U
#define GPIO_8_CANTXB                   0x00061002U
#define GPIO_8_ADCSOCAO                 0x00061003U
#define GPIO_8_EQEP3S                   0x00061005U
#define GPIO_8_SCITXDA                  0x00061006U

#define GPIO_9_GPIO9                    0x00061200U
#define GPIO_9_EPWM5B                   0x00061201U
#define GPIO_9_SCITXDB                  0x00061202U
#define GPIO_9_OUTPUTXBAR6              0x00061203U
#define GPIO_9_EQEP3I                   0x00061205U
#define GPIO_9_SCIRXDA                  0x00061206U

#define GPIO_10_GPIO10                   0x00061400U
#define GPIO_10_EPWM6A                   0x00061401U
#define GPIO_10_CANRXB                   0x00061402U
#define GPIO_10_ADCSOCBO                 0x00061403U
#define GPIO_10_EQEP1A                   0x00061405U
#define GPIO_10_SCITXDB                  0x00061406U
#define GPIO_10_UPP_WAIT                 0x0006140FU
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

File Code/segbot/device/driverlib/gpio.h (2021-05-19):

//###########################################################################
//
// FILE:   gpio.h
//
// TITLE:  C28x GPIO driver.
//
//###########################################################################
// $TI Release: F2837xD Support Library v3.10.00.00 $
// $Release Date: Tue May 26 17:13:46 IST 2020 $
// $Copyright:
// Copyright (C) 2013-2020 Texas Instruments Incorporated - http://www.ti.com/
//
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
//   Redistributions of source code must retain the above copyright 
//   notice, this list of conditions and the following disclaimer.
// 
//   Redistributions in binary form must reproduce the above copyright
//   notice, this list of conditions and the following disclaimer in the 
//   documentation and/or other materials provided with the   
//   distribution.
// 
//   Neither the name of Texas Instruments Incorporated nor the names of
//   its contributors may be used to endorse or promote products derived
//   from this software without specific prior written permission.
// 
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
#ifndef GPIO_H
#define GPIO_H

//*****************************************************************************
//
// If building with a C++ compiler, make all of the definitions in this header
// have a C binding.
//
//*****************************************************************************
#ifdef __cplusplus
extern "C"
{
#endif

//*****************************************************************************
//
//! \addtogroup gpio_api GPIO
//! @{
//
//*****************************************************************************

#include <stdbool.h>
#include <stdint.h>
#include "inc/hw_gpio.h"
#include "inc/hw_memmap.h"
#include "inc/hw_types.h"
#include "inc/hw_xint.h"
#include "cpu.h"
#include "xbar.h"
#include "debug.h"

//*****************************************************************************
//
// Useful defines used within the driver functions to access gpio registers.
// Not intended for use by application code.
//
// Divide by 2 is for C28x which has word access
//
//*****************************************************************************
#define GPIO_CTRL_REGS_STEP     ((GPIO_O_GPBCTRL - GPIO_O_GPACTRL) / 2U)
#define GPIO_DATA_REGS_STEP     ((GPIO_O_GPBDAT - GPIO_O_GPADAT) / 2U)

#define GPIO_GPxCTRL_INDEX      (GPIO_O_GPACTRL / 2U)
#define GPIO_GPxQSEL_INDEX      (GPIO_O_GPAQSEL1 / 2U)
#define GPIO_GPxMUX_INDEX       (GPIO_O_GPAMUX1 / 2U)
#define GPIO_GPxDIR_INDEX       (GPIO_O_GPADIR / 2U)
#define GPIO_GPxAMSEL_INDEX     (0x00000014U / 2U) // Address rsvd for GPAAMSEL
#define GPIO_GPxPUD_INDEX       (GPIO_O_GPAPUD / 2U)
#define GPIO_GPxINV_INDEX       (GPIO_O_GPAINV / 2U)
#define GPIO_GPxODR_INDEX       (GPIO_O_GPAODR / 2U)
#define GPIO_GPxGMUX_INDEX      (GPIO_O_GPAGMUX1 / 2U)
#define GPIO_GPxCSEL_INDEX      (GPIO_O_GPACSEL1 / 2U)
#define GPIO_GPxLOCK_INDEX      (GPIO_O_GPALOCK / 2U)
#define GPIO_GPxCR_INDEX        (GPIO_O_GPACR / 2U)

#define GPIO_GPxDAT_INDEX       (GPIO_O_GPADAT / 2U)
#define GPIO_GPxSET_INDEX       (GPIO_O_GPASET / 2U)
#define GPIO_GPxCLEAR_INDEX     (GPIO_O_GPACLEAR / 2U)
#define GPIO_GPxTOGGLE_INDEX    (GPIO_O_GPATOGGLE / 2U)

#define GPIO_MUX_TO_GMUX        (GPIO_O_GPAGMUX1 - GPIO_O_GPAMUX1)

#ifndef DOXYGEN_PDF_IGNORE
//*****************************************************************************
//
// Values that can be passed to GPIO_setPadConfig() as the pinType parameter
// and returned by GPIO_getPadConfig().
//
//*****************************************************************************
#define GPIO_PIN_TYPE_STD       0x0000U //!< Push-pull output or floating input
#define GPIO_PIN_TYPE_PULLUP    0x0001U //!< Pull-up enable for input
#define GPIO_PIN_TYPE_INVERT    0x0002U //!< Invert polarity on input
#define GPIO_PIN_TYPE_OD        0x0004U //!< Open-drain on output
#endif

//*****************************************************************************
//
//! Values that can be passed to GPIO_setDirectionMode() as the \e pinIO
//! parameter and returned from GPIO_getDirectionMode().
//
//*****************************************************************************
typedef enum
{
    GPIO_DIR_MODE_IN,                   //!< Pin is a GPIO input
    GPIO_DIR_MODE_OUT                   //!< Pin is a GPIO output
} GPIO_Direction;

//*****************************************************************************
//
//! Values that can be passed to GPIO_setInterruptType() as the \e intType
//! parameter and returned from GPIO_getInterruptType().
//
//*****************************************************************************
typedef enum
{
    GPIO_INT_TYPE_FALLING_EDGE = 0x00,   //!< Interrupt on falling edge
    GPIO_INT_TYPE_RISING_EDGE  = 0x04,   //!< Interrupt on rising edge
    GPIO_INT_TYPE_BOTH_EDGES   = 0x0C    //!< Interrupt on both edges
} GPIO_IntType;
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

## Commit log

2021-05-17 Add initial wiring diagram
2021-05-17 Add links to initial parts list and wiring diagram
2021-05-17 Add initial EagleCAD and Fusion data
    [Segbot_schematic_v1.brd, Segbot_schematic_v1.sch, segbot_frame.dwg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]
2021-05-17 Add simulations and reworked files
    [ME461_F28379D.brd, ME461_F28379D.sch, ME461_F28379DHeaders.brd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]
2021-05-19 Add reworked wiring diagram and update matlab equations
2021-05-19 Update reworked wiring
2021-05-19 Add details about wiring considerations
2021-05-19 Update wiring considerations
2021-05-25 Add comments to Kalman filter
